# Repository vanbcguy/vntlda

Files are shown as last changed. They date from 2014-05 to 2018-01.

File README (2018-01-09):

vntlda
======

VNT LDA Controller

This software is designed to let you build yourself a VNT controller using an Arduino.  At a minimum you can run this with just a pressure sensor or just a TPS sensor plus an RPM signal, though for actual closed loop control you need all three.  The software will also work with an EGT sensor and can control a second solenoid / device - this can be used to reduce the pressure seen by the LDA when you hit high EGTs thereby reducing fuel, or it could be used to control a water/methanol injector or really do anything you might be able to think of.

Suggested Pressure Sensors
==========================

The included board design is intended to be used with Freescale MPX-series pressure sensors.  Depending on what you want to do you can use either absolute or relative / gauge pressure sensors.  Modern vehicle controls almost universally use absolute pressure sensors - this results in higher gauge pressure numbers at high altitudes providing consistent performance, however that assumes the ECU is controlling other things like fueling too.  I personally have used relative pressure sensors - they will read '0' when off boost just like a traditional boost gauge would.  This is also how wastegate turbos work.  Given that you are building your own controller I'm guessing you aren't trying to comply with strict emissions control regulations so you'll probably find the relative sensors work just fine, plus you'll probably enjoy having all the potential power your vehicle could have at lower altitudes.

Here are some example sensors:

MPX4250DP - 2 port sensor (leave the bottom port open) - max pressure 36 PSI
MPX5500DP - 2 port sensor (leave the bottom port open) - max pressure 72 PSI

Use the lowest value sensor that will meet your needs - don't be tempted to just go for the
"biggest" you can get as the larger the range of the sensor the lower its resolution. I have
used the MPX4250DP for my boost measurements and the MPX5500DP for my EMP measurements.

Suggested TPS Sensor
====================

You need "something" that will provide varying resistance as the accelerator pedal moves.  If you are using this with a Bosch VE/VP style pump there are a few options available.  Some Dodge trucks with Cummins engines and automatic transmissions have a TPS sensor mounted to the pump already - if you control the automatic transmission some other way (like a knob on the dash) then you can use the TPS for this controller.  There are also Land Rover 300 TDI pumps that came with a Bosch TPS to control their EGR system - these should bolt on to most other VE pumps as well.  If you have a 300 TDI with the EGR otherwise removed then you are already most of the way there!  If you have a different style pump then you are on your own - I recommend finding a "cheap" TPS at a parts store that you think you can work with as that way getting replacement parts will be easy.  The Land Rover TPS is frigging expensive to buy new!

Suggested RPM Sensor
====================

The project I based this off of was designed to work with a Honeywell GT101DC.  I used the factory crank position sensor on my VW AHU TDI, this required me to add an extra IC to work with magnetic reluctance sensors.  You can re-use the board design with the Honeywell sensor just by not installing a few components, namely the TI IC and its associated resistors.  Then the Honeywell wire can be connected to the appropriate hole on the board, probably.

Suggested Boost Control Solenoids
=================================

I initially used the readily avaiable GM 3-port boost control solenoids - AC Delco part number 214-474.  They seem to work fine though they are a bit noisy - take care where you mount them (ie don't screw them to the firewall as the noise will drive you nuts).  I have since moved to a VW-style "N75" valve from a Mk4 TDI; these valves are much quieter.

Logging
=======

The system can stream live data via the serial port for logging purposes.  Press the '#' key while connected via serial and the system will start streaming data in this format:

mapCorrected,vntTargetPressure,vntPositionRemapped,tpsCorrected,rpmActual,pidOutput,n75precontrol,vntMinDc,vntMaxDc,mode,targetRatioKp,targetRatioKi,targetRatioKd,boostCalculatedP,boostCalculatedI,boostCalculatedD,temp1,auxOutput,millis( / 10)

The output data can be captured with a tool like 'screen' and logged to disk. It can then be opened directly in a spreadsheet program like LibreOffice or Excel for graphing purposes.

Updates
=======

Patches and updates very welcome! The code is currently "good enough" for to get things done; many improvements could be made. Assistance reducing memory usage, implementing the missing EMP stuff, etc would be well received.

Board Notes
===========

The header for the MAX31855 amplifier board really should be flipped the other way around - I made a mistake on the board layout. This can be overcome by soldering the header and terminals to the opposite side of the MAX31855 board from normal. Everthing works fine this way.

LCD Setup
=========

This program expects to see an Adafruit RGB serial LCD backpack. It also expects the serial LCD backpack to have been configured for 115200 baud already - the display will appear corrupted if the baud rate of the LCD does not match the program rate. While I have tested successfully at 9600 baud (the Adafruit default) by far the longest running part of the program is the actual LCD update routine - while the VNT control stuff takes only a couple of ms (even with lots of float divisions!) the LCD update takes about 26-28ms at 9600 baud. It takes only 2ms at 115200 so your controller will be much happier with the faster rate. Remember it cannot calculate anything while it's writing to the LCD!

To set the baud rate on a fresh serial backpack plug it in via USB. USB doesn't make use of the baud rate so you can set it up no matter what the current settings are. Issue the following commands:

# stty -F /dev/ttyACM0 9600 -parenb cs8 -cstopb -crtscts
# echo -e "\xFE\x39\x08" > /dev/ttyACM0

The baud rate setting is stored on the LCD's EEPROM and will be briefly displayed at startup allowing you to verify the setting was saved successfully.

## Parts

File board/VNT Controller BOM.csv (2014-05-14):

Part | Value | Device | Package | Description | PROD_ID
C1 | 0.33μF | CAPPTH | CAP-PTH-SMALL | Capacitor
C2 | 0.1μF | CAPPTH | CAP-PTH-SMALL | Capacitor
C3 | 470 pF | CAPPTH | CAP-PTH-SMALL | Capacitor
C4 | 470 pF | CAPPTH | CAP-PTH-SMALL | Capacitor
C5 | 0.01 μF | CAPPTH | CAP-PTH-SMALL | Capacitor
C6 | 1.0 μF | CAPPTH | CAP-PTH-SMALL | Capacitor
C7 | 0.01 μF | CAPPTH | CAP-PTH-SMALL | Capacitor
C8 | 1.0 μF | CAPPTH | CAP-PTH-SMALL | Capacitor
C9 | 0.01 μF | CAPPTH | CAP-PTH-SMALL | Capacitor
C10 | 0.01 μF | CAPPTH | CAP-PTH-SMALL | Capacitor
C11 | 0.33 μF | CAP_POLPTH2 | CPOL-RADIAL-10UF-25V | Capacitor Polarized
C12 | 330 pF | CAPPTH | CAP-PTH-SMALL | Capacitor
C14 | 0.1μF | CAPPTH | CAP-PTH-SMALL | Capacitor
C15 | 0.1μF | CAPPTH | CAP-PTH-SMALL | Capacitor
D1 | 1N4001 | DIODEPTH | DIODE-1N4001 | Diode
D2 | 1N4001 | DIODEPTH | DIODE-1N4001 | Diode
IC1 | LM7809 | V_REG_78XXSINK | TO220-IGO | Voltage Regulator
IC2 | LM1815 | DIL14S | SOCKET-14 | Dual In Line / Socket
JP1 |  | M07LOCK_LONGPADS | 1X07_LOCK_LONGPADS | Header 7
JP2 |  | M07LOCK_LONGPADS | 1X07_LOCK_LONGPADS | Header 7
JP3 | EGT | M06SIP_LOCK | 1X06-SIP_LOCK | Header 6
PS1 | MPX4250DP | MPX****-867C-H | 867C-H | Generic MPX pressure sensor
PS2 | MPX5500DP | MPX****-867C-H | 867C-H | Generic MPX pressure sensor
Q1 | MOSFET-NCHANNELFQP30N06L | MOSFET-NCHANNELFQP30N06L | TO220V | Common NMOSFET Parts | TRANS-10060
Q2 | MOSFET-NCHANNELFQP30N06L | MOSFET-NCHANNELFQP30N06L | TO220V | Common NMOSFET Parts | TRANS-10060
R1 | 82K | RESISTORPTH-1/4W-VERT | AXIAL-0.1 | Resistor
R2 | 1K | RESISTORPTH-1/4W-VERT | AXIAL-0.1 | Resistor
R3 | 4.7K | RESISTORPTH-1/4W-VERT | AXIAL-0.1 | Resistor
R4 | 18K | RESISTORPTH-1/4W-VERT | AXIAL-0.1 | Resistor
R5 | 1M | RESISTORPTH-1/4W-VERT | AXIAL-0.1 | Resistor
R6 | 100 | RESISTORPTH-1/4W-VERT | AXIAL-0.1 | Resistor
R7 | 100 | RESISTORPTH-1/4W-VERT | AXIAL-0.1 | Resistor
R8 | 10K | RESISTORPTH-1/4W-VERT | AXIAL-0.1 | Resistor
R9 | 10K | RESISTORPTH-1/4W-VERT | AXIAL-0.1 | Resistor
U$1 | ARDUINO_R3_SHIELD | ARDUINO_R3_SHIELD | UNO_R3_SHIELD | Shield form compatible with the Arduino Uno R3.

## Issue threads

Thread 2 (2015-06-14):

prog_uchar will not work any more

wickeddoc87, 2015-06-14:
Hello,

Nice to see this Project goes forward.
With the new Arduino IDE 1.6.4 "prog_uchar" will not work any more.
I replaced all "prog_uchar" with "const unsigned char".
Like this it is possible to compile the code with the new Arduino IDE, i will see next week if it is working correct.

I have designed a new PCB with SMD technology, If you are interested tell me how i can send it to you.

I have to questions about your code.
What exactly to you mean with EMP and AUX.

Thx alot,

best regards,
Peter

stupa55, 2015-06-15:
Hej there :)

Nice to here you still working on the project. I sold my VNT turbo to a friend along with the Arduino controller and got back a Wastegate turbo. We set it up and using the one old version of the code and it does work great. Setting the VNT with one driver and a passenger is much easier than I done before alone lol :D
Best reagrdsRemi

     wickeddoc87 <notifications@github.com> schrieb am 12:40 Sonntag, 14.Juni 2015:

 Hello, Nice to see this Project goes forward.
With the new Arduino IDE 1.6.4 "prog_uchar" will not work any more.
I replaced all "prog_uchar" with "const unsigned char".
Like this it is possible to compile the code with the new Arduino IDE, i will see next week if it is working correct.I have designed a new PCB with SMD technology, If you are interested tell me how i can send it to you.I have to questions about your code.
What exactly to you mean with EMP and AUX.Thx alot, best regards,
Peter—
Reply to this email directly or view it on GitHub.

wickeddoc87, 2015-06-18:
Does we know us?
Why your frind use the first version now?

@the author
why you use so many floats in your code. I changed all floats to byte, int  and longs. It's not useful to do calculations with floats.  So I try to keep all variables as big as possible and just before we write it to the output  I calculate the true value. Like this I don't need one float at all.

Just in the Part for Human visualisation I use floats for Ki, Kd, kp...

Why you use micros for the RPM Trigger?  Even if you're engine have 10000 RPMs and you use 6 teeth,  the RPM resolution would be still 1ms,  so Millis should be enough.

An older Projects shows me that micros and floats are slowing down the processor extremely.

Best regards
Peter

.

Best regards Peter

wickeddoc87, 2015-06-19:
Hello, it's me again....

You're calculating controls.lastTime with Millis.
Your loop take about 0.56ms.  So as I understand the code controls.lastTime will be almost ever 1 and sometimes 0 if you do the calculation with multiplication 0 integral is 0.  I think at this position we should do the calculation with micros instead of Millis.

Best regards Peter.

stupa55, 2015-06-19:
Hi, there about which code are we talking ??
I haven't written the code I only used it from vanbcguy, the first code I used and that worked good for me was before 24th Dec 2014 :)
I haven't done further inspections cause all in all the DMN code which vanbcguy based on worked also awesome but needed better adaptation. I used the first versions of vanbcguy to compare and it worked much smoother in my opinion.

Remi

     wickeddoc87 <notifications@github.com> schrieb am 11:17 Freitag, 19.Juni 2015:

 Hello, it's me again.... You're calculating controls.lastTime with Millis.
Your loop take about 0.56ms. So as I understand the code controls.lastTime will be almost ever 1 and sometimes 0 if you do the calculation with multiplication 0 integral is 0. I think at this position we should do the calculation with micros instead of Millis. Best regards Peter. —
Reply to this email directly or view it on GitHub.

vanbcguy, 2015-06-19:
millis is not updated when certain other things are happening, micros always is.

The control loop doesn't execute every run, only every 80ms.

very happy to hear about the update for 1.6.4 - I hadn't had a chance to look at that yet.

EMP = exhaust manifold pressure.  I have a sensor on my board for it but I haven't done anything with it yet.  It is only partly there in the code, it is basically unimplemented at the moment.

The AUX output can be used for controlling water/meth, I use it to help limit EGTs by hiding boost from the LDA.  I have it set to start opening a second control solenoid as EGTs approach 800C.

wickeddoc87, 2015-06-19:
thx for explaining.....

RPM Value is unstable the reason for it is a semi. fault.

  if (teethNo > rpmResolution); <--------------- This Semi should not be there.
  {

wickeddoc87, 2015-06-20:
The Arduino does not support an Software pull down on Inputs .. so this will not work

  pinMode(PIN_TPS, INPUT);
  pinMode(PIN_MAP, INPUT);

  digitalWrite(PIN_TPS, LOW); // safety unconnected TPS
  digitalWrite(PIN_MAP, HIGH); // safety unconnected MAP

you have to do the Pulldown external with a resistor 100K maybe.

so the setup can look like this.

  pinMode(PIN_TPS, INPUT);
  pinMode(PIN_MAP, INPUT_PULLUP);

vanbcguy, 2015-06-22:
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

Good catch.  I've updated, will test this afternoon.

Madhair, 2015-07-04:
hi guys

hope ye can help me out here. new to arduino programming etc but very keen to learn. ive been trying to verify the .ino file but a load of the "prog_uchar" errors were coming up so i replaced them with "const unsigned char" as mentioned above and they're all gone now :)

here is the list of errors i have now and im stumped. i cant figure this part out at all :/ any chance of some help?

Arduino: 1.6.5 (Mac OS X), Board: "Arduino Leonardo"

Build options changed, rebuilding all
vnt_lda_myPID_1.ino: In function 'void setPwmFrequency(int, int)':
vnt_lda_myPID_1:384: error: 'TCCR2B' was not declared in this scope
'TCCR2B' was not declared in this scope

cheers in advance :)

Shane

Madhair, 2015-07-04:
think i have it!

bit of info with leonardo having a library compatibility issue here in post 8
http://forum.arduino.cc/index.php?topic=175158.0

i swapped TCCR2B in line 384 to TCCR0B and it verified. ill report back (if ye dont mind :P) during the week when i get the chance to fit to the car :)

vanbcguy, 2015-07-09:
I've committed the prog_uchar change so it's there for everyone. :)

The 'TCCR2B' to 'TCCR0B' change alters the PWM timers.  The 'setPwmFrequency' routine is specifically set up for the regular 'Uno' so it may need adjustment for other boards.  The frequency that's set in my code is correct for the specific GM solenoids I'm using (which like a sllloowww low frequency signal); other solenoids don't necessarily want the same thing.

vanbcguy, 2015-07-09:
@wickeddoc87 - I'd be interested to see your version without using floats so heavily.  I know it's kind of crappy right now.

The main slowdown though is actually updating the LCD - it takes nearly 50ms to update the entire thing.  I recently changed it to update half the screen at a time which got it down to 28ms per update, but that's really what is limiting how fast I can run the loop right now.  I need to spend some time and sort it out so it can just blast out an entire line at once rather than doing so many positioning steps, just haven't had a chance.

wickeddoc87, 2015-07-09:
Good morning,

about Speed... i did same "Benchmarks" with old and new Arduino IDE and relatively simple Code. The Device programmed with the Arduino IDE 1.6.4 works a LOT LOT LOT faster than 1.0.5, maybe you should try an Update.

About the version without float.... i tried a complete other CALC Part Yesterday and "destroyed" the "old code" without doing a new Backup.  i Just have a not finished old Backup...

void processValues() {

  controls.vntMaxDc = mapLookUp(boostDCMax, controls.rpmCorrected, controls.tpsCorrected);
  controls.vntMinDc = mapLookUp(boostDCMin, controls.rpmCorrected, controls.tpsCorrected);

  controls.rpmCorrected = mapValues(controls.rpmActual, 0, settings.rpmMax);
  controls.mapInput = getFilteredAvarage(&mapAvg);
  controls.mapCorrected = mapValues(controls.mapInput, settings.mapMin, settings.mapMax);
  controls.tpsInput = getFilteredAvarage(&tpsAvg);
  controls.tpsCorrected = mapValues(controls.tpsInput, settings.tpsMin, settings.tpsMax);
  controls.empInput = getFilteredAvarage(&empAvg);
  controls.empCorrected = mapValues(controls.empInput, settings.empMin, settings.empMax);
  controls.egtCorrected = mapValues(controls.temp1, settings.egtMin, settings.egtMax);

  // EGT controls
  controls.auxOutput = mapLookUp(auxMap, controls.rpmCorrected, controls.egtCorrected);

  // TODO add RPM hysterisis
  if ( controls.tpsCorrected > 0 ) {
    controls.idling = false;
  }
  else if ( controls.rpmActual < IDLE_MAX_RPM ) {
    controls.idling = true;
  }
  else {
    controls.idling = false;
  }
  unsigned long currentMillis = millis();
  long timeChange = currentMillis - controls.lastTime;

  long error;
  long integral;
  int calc_integral;
  long derivate;

  int controlSpan;
  int scaledInput;
  int scaledTarget;
  int toControlVNT;
  boolean everyThingIsNormal;

 if (!(controls.prevPidOutput >= 254 && error > 0) && !(controls.prevPidOutput <= 0 && error < 0))  everyThingIsNormal == true;
 else  everyThingIsNormal == false;

  /* This is the available span of our DC - we can only go between min and max */
  controlSpan = controls.vntMaxDc - controls.vntMinDc;

  scaledInput = controls.mapCorrected;

  if (scaledInput > 255) scaledInput = 255;
  else if (scaledInput < 0) scaledInput = 0;

  if ((controls.idling)) {
    // If we are at idle then we don't want any boost regardless of map
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
wickeddoc87, 2015-07-09:
I don't know your display,
I use a Sparkfun Serial Display, it works with Baudrates up to 38400

If your Display Update takes 50ms... with Baud 9600 it will only take 13ms with Baud 38400...

wickeddoc87, 2015-08-05:
I found the real Performance Killer!
It is the max31855 library!

The Library works with Floats und is unbelievable slow!
there are other Library's for the max31855!

With deactivated EGT my Code works 3Times Faster....

I Hope this will help you!

Best regards,
Peter

wickeddoc87, 2015-08-05:
Just try...  To see the Difference..

void readValuesEgt() {
 //  controls.temp1 = thermocouple.readCelsius();
  // controls.temp2 = toTemperature(analogRead(PIN_TEMP2)/4);
  controls.temp2 = 0; // disabled for now as we aren't using it

  if (controls.temp1<=0) {
    controls.temp1 = 0;
  }
  else if (controls.temp1 >= settings.egtMax) {
    controls.temp1 = settings.egtMax;
  }

}

vanbcguy, 2015-08-05:
Yes, it's terrible eh? Actually I'm running a patched version of that library that dramatically speeds it up.  There are many delay_ms calls that are slowing things down more than necessary; this code block is the troublemaker - I've changed the delay_ms to delay_us.  I found that I got bad temperature readings unless I increased the delay to 10 us rather than 1 us.

uint32_t Adafruit_MAX31855::spiread32(void) {
  int i;
  uint32_t d = 0;

  if(hSPI) {
    return hspiread32();
  }

  digitalWrite(sclk, LOW);
  _delay_us(10);
  digitalWrite(cs, LOW);
  _delay_us(10);

  for (i=31; i>=0; i--)
  {
    digitalWrite(sclk, LOW);
    _delay_us(10);
    d <<= 1;
    if (digitalRead(miso)) {
      d |= 1;
    }

    digitalWrite(sclk, HIGH);
    _delay_us(1);
  }

  digitalWrite(cs, HIGH);
  //Serial.println(d, HEX);
  return d;
}

I did actually try a few other MAX31855 libraries but the timer settings I use to get the right PWM frequency seem to cause the EGT readings to get cut in half.  This was the only library I could get to spit out the correct value.

vanbcguy, 2017-11-20:
As we've changed MAX31855 libraries, resolved the prog_uchar issues and switched to a totally different PID routine I'm marking this as closed...

Closed 2017-11-20.

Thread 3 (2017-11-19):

CAN BUS communication ?

HaganHao, 2017-11-19:
I have a actuator from Hella, which is defined to communicate with ECU by CAN-BUS.
How can I control my actuator with those code ?

vanbcguy, 2017-11-20:
You would have to build a CANBUS interface; there's nothing in the code designed to do that currently. I believe I have seen CANBUS shields out there however I don't have a CANBUS turbo to test with. Patches happily accepted!

Closed 2017-11-20.

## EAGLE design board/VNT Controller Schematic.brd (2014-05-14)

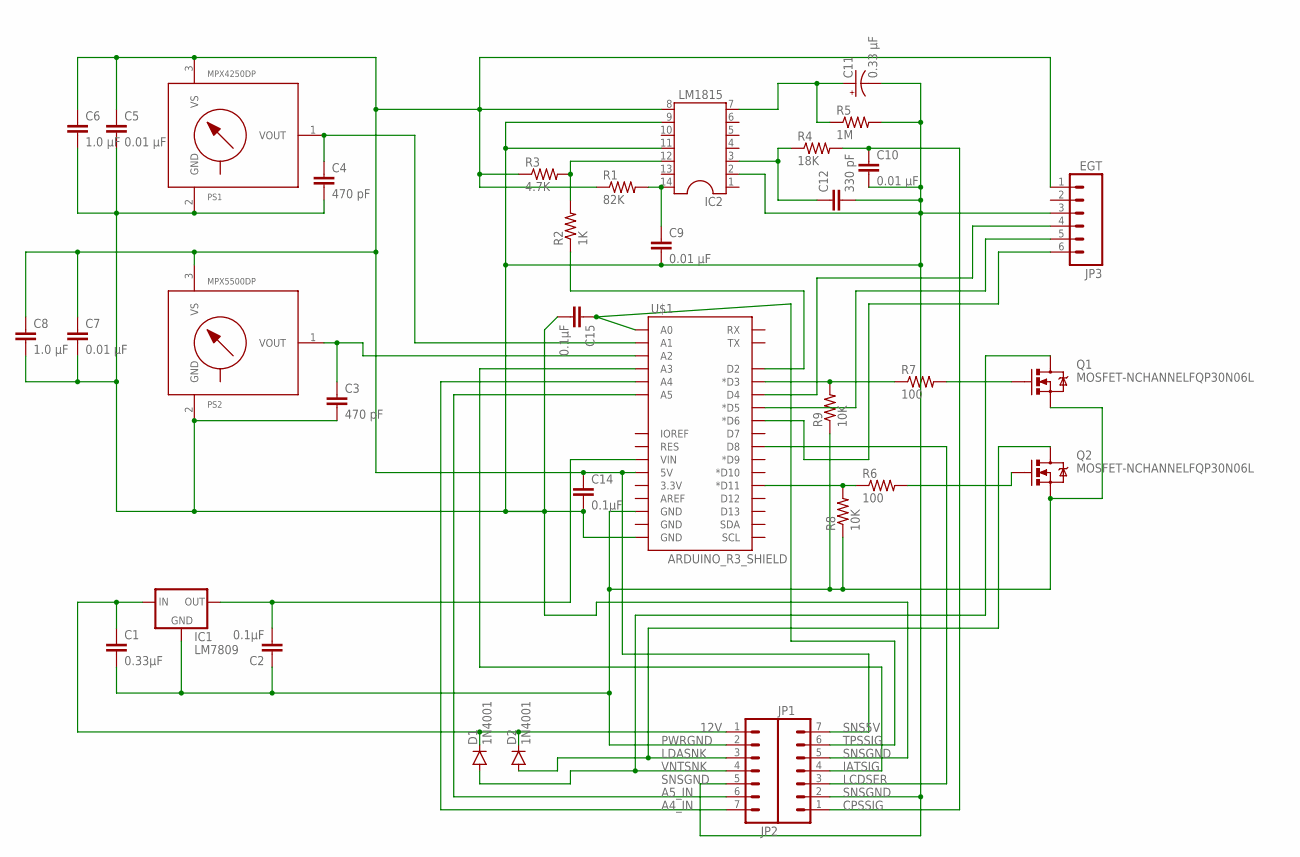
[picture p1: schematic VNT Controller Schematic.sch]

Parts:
C1: 0.33μF; CAP-PTH-SMALL
C2, C14, C15: 0.1μF; CAP-PTH-SMALL
C3, C4: 470 pF; CAP-PTH-SMALL
C5, C7, C9, C10: 0.01 μF; CAP-PTH-SMALL
C6, C8: 1.0 μF; CAP-PTH-SMALL
C11: 0.33 μF; CPOL-RADIAL-10UF-25V
C12: 330 pF; CAP-PTH-SMALL
D1, D2: 1N4001; DIODE-1N4001
IC1: LM7809; TO220-IGO
IC2: LM1815; SOCKET-14
JP1, JP2: M07LOCK_LONGPADS; 1X07_LOCK_LONGPADS
JP3: EGT; 1X06-SIP_LOCK
PS1: MPX4250DP; 867C-H
PS2: MPX5500DP; 867C-H
Q1, Q2: MOSFET-NCHANNELFQP30N06L; TO220V
R1: 82K; AXIAL-0.1
R2: 1K; AXIAL-0.1
R3: 4.7K; AXIAL-0.1
R4: 18K; AXIAL-0.1
R5: 1M; AXIAL-0.1
R6, R7: 100; AXIAL-0.1
R8, R9: 10K; AXIAL-0.1
U$1: ARDUINO_R3_SHIELD; UNO_R3_SHIELD

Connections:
12V: C1.1, D1.C, D2.C, IC1.IN, JP2.1
A4_IN: JP2.7, U$1.A4
A5_IN: JP2.6, U$1.A5
CPSSIG: C10.1, JP1.1, R4.P$2 (2)
IATSIG: JP1.4, U$1.A3
LCDSER: JP1.3, U$1.D8
LDASNK: D2.A, JP2.3, Q2.2 (D)
unnamed: R6.P$1 (1), R8.P$2 (2), U$1.D11 (*D11)
unnamed: C3.1, PS2.1 (VOUT), U$1.A2
unnamed: Q2.1 (G), R6.P$2 (2)
unnamed: IC2.12, R2.P$2 (2), R3.P$2 (2)
unnamed: C4.1, PS1.1 (VOUT), U$1.A1
unnamed: R2.P$1 (1), U$1.D2
unnamed: C9.1, IC2.14, R1.P$2 (2)
unnamed: R7.P$1 (1), R9.P$2 (2), U$1.D3 (*D3)
unnamed: C2.2, IC1.OUT, U$1.VIN
unnamed: Q1.1 (G), R7.P$2 (2)
unnamed: C11.1 (+), IC2.7, R5.P$1 (1)
unnamed: JP3.4, U$1.D4
unnamed: JP3.5, U$1.D5 (*D5)
unnamed: C12.1, IC2.3, R4.P$1 (1)
unnamed: JP3.6, U$1.D6 (*D6)
PWRGND: C1.2, C2.1, IC1.GND, JP2.2, Q1.3 (S), Q2.3 (S), R8.P$1 (1), R9.P$1 (1), U$1.GND@2 (GND)
SNS5V: C5.1, C6.1, C7.1, C8.1, C14.1, IC2.8, JP1.7, JP3.1, PS1.3 (VS), PS2.3 (VS), R1.P$1 (1), R3.P$1 (1), U$1.5V
SNSGND: C3.2, C4.2, C5.2, C6.2, C7.2, C8.2, C9.2, C10.2, C11.2 (-), C12.2, C14.2, C15.2, IC2.2, IC2.9, IC2.11, JP1.2, JP1.5, JP2.5, JP3.3, PS1.2 (GND), PS2.2 (GND), R5.P$2 (2), U$1.GND@0 (GND)
TPSSIG: C15.1, JP1.6, U$1.A0
VNTSNK: D1.A, JP2.4, Q1.2 (D)

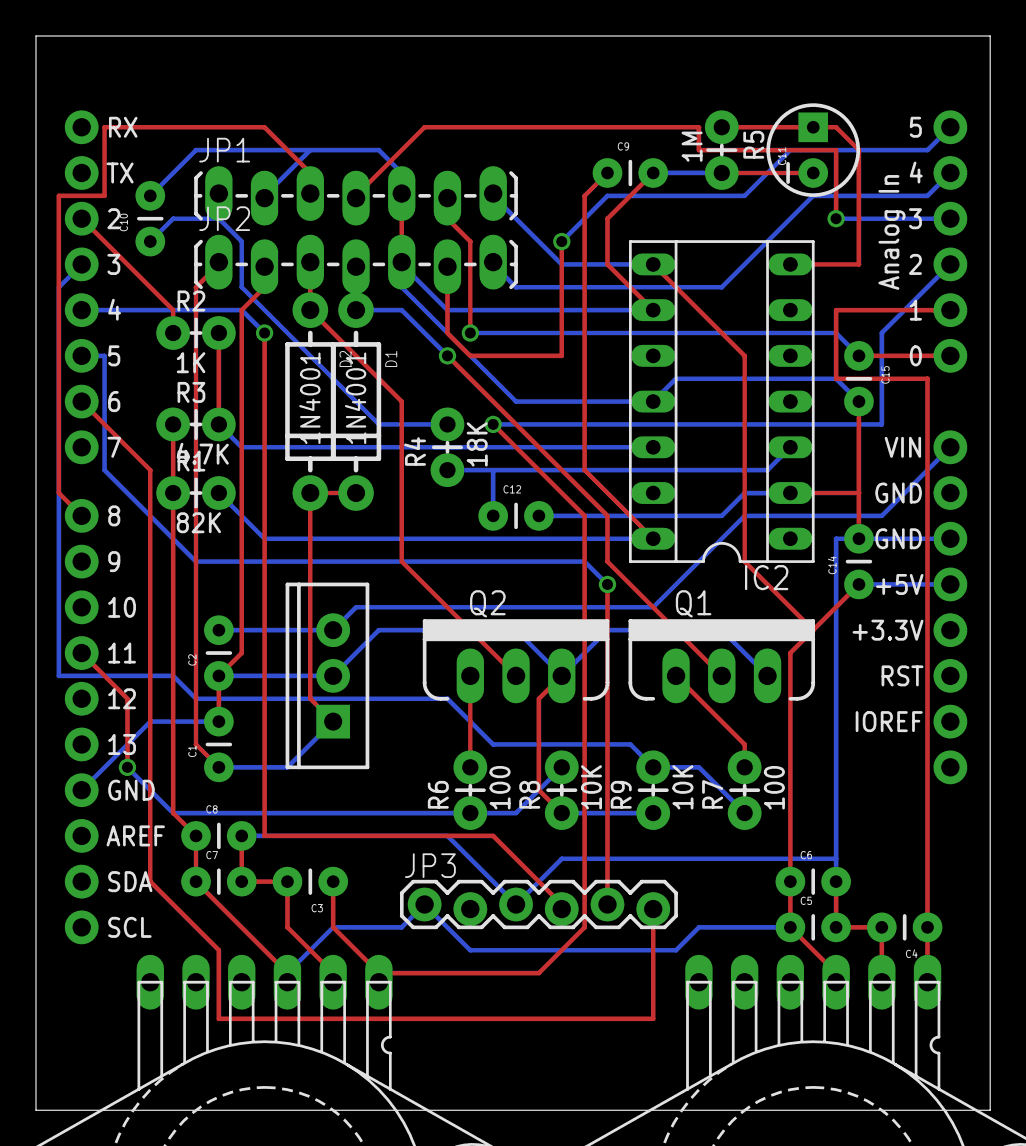
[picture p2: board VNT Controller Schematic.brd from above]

Board: 2 copper layers, 53.0 x 59.7 mm, 35 parts (0 on the bottom side), 27 nets.

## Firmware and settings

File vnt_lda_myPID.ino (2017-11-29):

/*
  Vanbcguy VNT LDA Controller - based on "Standalone VNT Controller" by DMN - http://dmn.kuulalaakeri.org/vnt-lda/
  My current code: https://github.com/vanbcguy/vntlda
  - Rewritten PID loop
  - Support added for EGT probe with LDA control based on EGTs
  - Other various small changes

*/

#include <avr/pgmspace.h>
#include <EEPROM.h>
#include <Wire.h>
#include <SoftwareSerial.h>
#include <SPI.h>
#include <MAX31855.h>    // Use library written for a faster read time - https://github.com/engineertype/MAX31855
#include <ResponsiveAnalogRead.h>
#include <PID_v1.h>

// Also used in NVRAM data store magic header
const unsigned char versionString[] PROGMEM  = "DMN-Vanbcguy Boost Ctrl v3.2.3";

#define PIN_BUTTON A5
#define PIN_HEARTBEAT 13

#define PIN_MAP A1
#define PIN_TPS A0
#define PIN_EMP A2

#define PIN_RPM_TRIGGER 2
#define PIN_VNT_N75 11
#define PIN_AUX_N75 3

#define PIN_LCD 8

#define LCD_BAUD_RATE 115200

// Pins for the EGT MAX31855
#define doPin 4
#define csPin 5
#define clPin 6

ResponsiveAnalogRead map_read(PIN_MAP, false);  // no sleep on the MAP read; need the resolution
ResponsiveAnalogRead tps_read(PIN_TPS, true);
ResponsiveAnalogRead rpm_read(0, true);

// Set up the LCD pin
SoftwareSerial lcd = SoftwareSerial(0, PIN_LCD);

// Set up the thermocouple pins (Adafruit MAX31855 thermocouple interface)
MAX31855 temp(doPin, csPin, clPin );

#define EGT_COOL 165
#define EGT_WARN 700
#define EGT_ALARM 775
#define EGT_MAX_READ 1101

#define IDLE_MAX_RPM 1150
#define MIN_BOOST_SPOOLED 10 // kPa
#define PID_CUT_IN 1520 // rpm
#define TPS_CUT_IN 18 // ~ 7%


/* Scaling factor for your sensors - 255 divided by this should equal the full scale deflection of your sensor */
#define MAP_SCALING_KPA 0.977
#define EMP_SCALING_KPA 1.953

/* Change this if you need to adjust the scaling of the PID outputs - ie if you need finer control at smaller fractional numbers increase this
  or if you need to have large multipliers then decrease this */
#define PIDControlRatio 300

/* The resolution we use to calculate RPM - we are only going to calculate RPM ever 'n' number of teeth that pass by; otherwise we are going to have
  a jittery value.  Divide this value by the 'Teeth per Rotation' setting to know how many revolutions before we caculate RPM. */
#define rpmResolution 30

// Set loop delay times
#define SERIAL_DELAY 107 // ms
#define EXEC_DELAY 50 //ms
#define DISPLAY_DELAY 250 // ms
#define MAP_DELAY 10 //ms


// Calculate Average values
#define AVG_MAX 15

#define MAP_AXIS_TPS 0xDE
#define MAP_AXIS_RPM 0xAD
#define MAP_AXIS_KPA 0xDD
#define MAP_AXIS_CELSIUS 0xAA
#define MAP_AXIS_VOLTAGE 0xAB
#define MAP_AXIS_DUTY_CYCLE 0xAC
#define MAP_AXIS_RAW 0x0
#define MAP_AXIS_EGT 0xAE

/*
  MAP format:

  'M','2','D'   // D - interpolated maps, d - nearest neighbor
  xsize,ysize,x-axis-type,y-axis-type,output-type,
  data[xsize,ysize],
  lastX,lastY,lastRet // automatically filled when used mapLookup

*/

unsigned char auxMap[] = {
  'M', '2', 'D',
  0x6, 0x8, MAP_AXIS_RPM, MAP_AXIS_EGT, MAP_AXIS_DUTY_CYCLE, // 01 - new version
  0, 0, 0, 0, 0, 0,
  0, 0, 0, 0, 0, 0,
  0, 0, 0, 0, 0, 0,
  0, 0, 0, 0, 0, 0,
  0, 0, 0, 0, 0, 0,
  0, 0, 0, 0, 0, 0,
  60, 60, 60, 60, 210, 210,
  210, 210, 210, 210, 210, 210,
  00, 00, 00,                // lastX,lastY,lastRet
};


unsigned char boostRequest[] = {
  'M', '2', 'D',
  0xC, 0xB, MAP_AXIS_RPM, MAP_AXIS_TPS, MAP_AXIS_KPA, // 01 - new version
  0, 0, 0, 15, 34, 44, 46, 46, 46, 43, 39, 37,
  0, 5, 15, 27, 38, 49, 51, 51, 51, 48, 43, 41,
  0, 5, 20, 32, 42, 54, 57, 57, 57, 53, 48, 45,
  0, 5, 20, 40, 55, 60, 63, 63, 63, 59, 53, 50,
  0, 5, 22, 43, 60, 67, 70, 70, 70, 65, 59, 55,
  0, 5, 24, 47, 65, 74, 78, 78, 78, 72, 66, 61,
  0, 6, 27, 58, 75, 92, 98, 98, 98, 90, 83, 76,
  0, 7, 30, 70, 92, 110, 123, 123, 123, 113, 104, 95,
  0, 9, 33, 75, 112, 138, 154, 154, 154, 141, 130, 119,
  0, 11, 41, 87, 128, 173, 193, 193, 193, 176, 162, 149,
  0, 12, 45, 85, 145, 192, 214, 214, 214, 195, 180, 166,
  00, 00, 00,                // lastX,lastY,lastRet
};

unsigned char boostDCMax[] = {
  'M', '2', 'D',
  0x8, 0xB, MAP_AXIS_RPM, MAP_AXIS_TPS, MAP_AXIS_DUTY_CYCLE,
  0, 204, 204, 180, 155, 140, 120, 70,
  0, 204, 204, 180, 155, 140, 120, 70,
  0, 204, 204, 175, 155, 140, 120, 70,
  0, 204, 190, 160, 135, 130, 120, 70,
  0, 204, 185, 160, 135, 130, 120, 70,
  0, 204, 180, 160, 135, 130, 120, 70,
  0, 204, 180, 155, 135, 130, 120, 70,
  0, 204, 175, 150, 135, 130, 120, 70,
  0, 204, 175, 145, 135, 125, 120, 70,
  0, 204, 180, 145, 135, 125, 120, 70,
  0, 204, 185, 145, 135, 125, 120, 70,
  00, 00, 00,                // lastX,lastY,lastRet
};

unsigned char boostDCMin[] = {
  'M', '2', 'D',
  0x9, 0xB, MAP_AXIS_RPM, MAP_AXIS_TPS, MAP_AXIS_DUTY_CYCLE,
  0, 50, 50, 50, 50, 50, 50, 50, 50,
  0, 121, 110, 100, 91, 83, 75, 68, 50,
  0, 121, 110, 100, 91, 83, 75, 68, 50,
  0, 121, 110, 100, 91, 83, 75, 68, 50,
  0, 110, 100, 91, 83, 75, 68, 62, 50,
  0, 99, 90, 70, 70, 70, 70, 65, 50,
  0, 99, 90, 70, 70, 70, 70, 65, 50,
  0, 99, 90, 70, 70, 70, 70, 65, 50,
  0, 99, 90, 70, 70, 70, 70, 65, 50,
  0, 99, 90, 70, 70, 70, 70, 65, 50,
  0, 99, 90, 70, 70, 70, 70, 65, 50,
  00, 00, 00,                // lastX,lastY,lastRet
};

unsigned char n75precontrolMap[] = {
  'M', '2', 'D',
  0xC, 0xB, MAP_AXIS_RPM, MAP_AXIS_TPS, MAP_AXIS_DUTY_CYCLE,
  0, 90, 90, 110, 110, 100, 90, 75, 62, 50, 50, 50,
  0, 204, 204, 204, 182, 163, 145, 130, 122, 115, 106, 70,
  0, 204, 204, 198, 165, 148, 137, 126, 118, 112, 102, 70,
  0, 204, 204, 176, 160, 142, 130, 117, 107, 102, 95, 70,
  0, 204, 204, 145, 124, 115, 109, 101, 94, 87, 82, 70,
  0, 204, 204, 145, 115, 112, 104, 94, 90, 85, 78, 70,
  0, 204, 204, 132, 111, 109, 103, 94, 87, 80, 76, 70,
  0, 204, 204, 132, 110, 108, 102, 94, 86, 80, 76, 70,
  0, 204, 204, 138, 107, 103, 98, 91, 85, 80, 76, 70,
  0, 204, 204, 142, 128, 119, 110, 103, 97, 89, 82, 70,
  0, 204, 204, 160, 150, 140, 132, 121, 110, 98, 86, 70,
  00, 00, 00,              // lastX,lastY,lastRet
};

const unsigned char statusString1[] PROGMEM  = " Active view: ";

#define OPTIONS_VANESOPENIDLE 1
#define OPTIONS_VNTOUTPUTINVERTED 2

// contains configurable data. Can be stored in eeprom
struct settingsStruct {
  int tpsMin;
  int tpsMax;
  int mapMin;
  int mapMax;
  int egtMin;
  int egtMax;
  int empMin;
  int empMax;
  int rpmMax;
  int rpmTeethsPerRotation;
  unsigned char mode;
  char options;
  int boostKp;
  int boostKi;
  int boostKd;
};

settingsStruct settings;

//  contains calculated output data. calculated each run of mainloop
struct controlsStruct {
  // inputs
  volatile int tpsInput;
  unsigned char tpsCorrected;
  volatile int mapInput;
  double mapCorrected;
  volatile int egtInput;
  unsigned char egtCorrected;
  volatile int empInput;
  unsigned char empCorrected;
  char mode; // operating mode

  // outputs

  double vntTargetPressure;
  unsigned char vntPositionRemapped;
  unsigned char vntPositionDC;
  int vntMinDc;
  int vntMaxDc;
  int n75precontrol;

  // calculated value
  volatile int rpmActual;
  volatile unsigned char rpmCorrected;
  unsigned char statusBits;

  bool idling;
  int temp1;

  unsigned char auxOutput;

  float boostCalculatedP;
  float boostCalculatedI;
  float boostCalculatedD;

  double pidOutput;

  unsigned long lastTime;
  float lastInput;
};

controlsStruct controls;


double Kp;
double Ki;
double Kd;

// set up VNT PID control
PID vntPid(&controls.mapCorrected, &controls.pidOutput, &controls.vntTargetPressure, Kp, Ki, Kd, P_ON_E,DIRECT);

struct avgStruct {
  unsigned char pos;
  unsigned char size;
  volatile unsigned int avgData[AVG_MAX];
};

avgStruct mapAvg;

char buffer[100]; // general purpose buffer, mainly used for string storage when printing from flash
unsigned long lastPacketTime;
const unsigned char mapVisualitionHelp[] PROGMEM  = "Top Left is 0,0 (press: L - toggle live mode)";

unsigned char page = 0;
const char *pages[] = {
  "About", "Adaptation", "Actuator Fine-tune", "Edit map: boostRequest", "Edit map: boostDCMin", "Edit map: boostDCMax", "Edit map: n75preControl", "Edit map: Aux. device PWM map", "Output Tests"
};

unsigned char *editorMaps[] = {
  boostRequest, boostDCMin, boostDCMax, n75precontrolMap, auxMap
};

unsigned char clearScreen[] =  {
  27, '[', '2', 'J', 27, '[', 'H'
};

const unsigned char ANSIclearEol[] PROGMEM = {
  27, '[', 'K', 0
};

const unsigned char ANSIclearEolAndLf[] PROGMEM = {
  27, '[', 'K', '\r', '\n', 0
};
const unsigned char ANSIgoHome[] PROGMEM = {
  27, '[', '1', ';', '1', 'H', 0
};
const unsigned char ANSIclearEos[] PROGMEM = {
  27, '[', 'J', 0
};

void setPwmFrequency(int pin, int divisor) {
  byte mode;
  if (pin == 5 || pin == 6 || pin == 9 || pin == 10) {
    switch (divisor) {
      case 1:
        mode = 0x01;
        break;
      case 8:
        mode = 0x02;
        break;
      case 64:
        mode = 0x03;
        break;
      case 256:
        mode = 0x04;
        break;
      case 1024:
        mode = 0x05;
        break;
      default:
        return;
    }
    if (pin == 5 || pin == 6) {
      TCCR0B = TCCR0B & 0b11111000 | mode;
    }
    else {
      TCCR1B = TCCR1B & 0b11111000 | mode;
    }
  }
  else if (pin == 3 || pin == 11) {
    switch (divisor) {
      case 1:
        mode = 0x01;
        break;
      case 8:
        mode = 0x02;
        break;
      case 32:
        mode = 0x03;
        break;
      case 64:
        mode = 0x04;
        break;
      case 128:
        mode = 0x05;
        break;
      case 256:
        mode = 0x06;
        break;
      case 1024:
        mode = 0x7;
        break;
      default:
        return;
    }
    // TCCR2A = 0xA3;
    TCCR2B = TCCR2B & 0b11111000 | mode;
  }
}


volatile unsigned int teethNo = 0;

void rpmTrigger() {
  // increase the tooth count whenever we see a tooth go by
  teethNo++;
}

unsigned long rpmMicros = 0;
unsigned long teethSeconds = 0;

void calcRpm() {
  if (teethNo > rpmResolution)
  {
    int rpm;

    detachInterrupt(0); // don't trigger increments while we're calculating

    teethSeconds = 60000000 / settings.rpmTeethsPerRotation;

    // teethSeconds is one second in microseconds / number of teeth per revolution - avoid overflowing by pre-dividing a second by the number of teeth
    rpm = (teethSeconds * teethNo) / (micros() - rpmMicros);

    // Set time to now, reset tooth count to zero to start incrementing again
    rpmMicros = micros();
    teethNo = 0;

    attachInterrupt(0, rpmTrigger, FALLING); // back to the daily grind

    // controls.rpmActual = (rpmSmoothing * rpm) + ((1.0-rpmSmoothing)*controls.rpmActual);

    rpm_read.update(rpm / 10);
    controls.rpmActual = rpm_read.getValue() * 10;

    if (controls.rpmActual > settings.rpmMax) {
      controls.rpmActual = 0;
    }
  }
}

void gotoXY(char x, char y) {
  Serial.print(F("\e["));
  Serial.print(y, DEC);
  Serial.print(F(";"));
  Serial.print(x, DEC);
  Serial.print(F("H"));
}

void setup_lcd() {
  // Put all the LCD setup stuff here, we will call this from
  // the "setup" loop

  lcd.begin(LCD_BAUD_RATE);

  // set the splash screen
  lcd.write(0xFE);
  lcd.write(0x40);
  strcpy_P(buffer, (PGM_P)&versionString);
  lcd.print(buffer);
  delay(10);


  // set the contrast, 200 is a good place to start, adjust as desired
  lcd.write(0xFE);
  lcd.write(0x50);
  lcd.write(200);
  delay(10);

  // set the brightness - we'll max it (255 is max brightness)
  lcd.write(0xFE);
  lcd.write(0x99);
  lcd.write(255);
  delay(10);

  // set background colour - r/g/b 0-255
  lcd.write(0xFE);
  lcd.write(0xD0);
  lcd.write(64);
  lcd.write(255);
  lcd.write((uint8_t)0);
  delay(10);

  // turn off cursors
  lcd.write(0xFE);
  lcd.write(0x4B);
  lcd.write(0xFE);
  lcd.write(0x54);

  // turn off autoscroll
  lcd.write(0xFE);
  lcd.write(0x52);

  // clear screen
  lcd.write(0xFE);
  lcd.write(0x58);
  delay(10);   // we suggest putting delays after each command

  // go 'home'
  lcd.write(0xFE);
  lcd.write(0x48);
  delay(10);   // we suggest putting delays after each command

  vntPid.SetSampleTime(100);
}

void calcKp() {
  Kp = (float)(settings.boostKp) / PIDControlRatio;
}

void calcKi() {
  Ki = (float)(settings.boostKi) / PIDControlRatio;
}

void calcKd() {
  Kd = (float)(settings.boostKd) / PIDControlRatio;
}

void setup() {
  delay(1500);    // Wait for LCD to actually start up
  setup_lcd();

  Serial.begin(115200);
  Serial.print(F("Boot:"));

  pinMode(PIN_HEARTBEAT, OUTPUT); // DEBUG led

  pinMode(PIN_BUTTON, INPUT); // Reset switch
  digitalWrite(PIN_BUTTON, HIGH);  // activate pull up resistor

  pinMode(PIN_RPM_TRIGGER, INPUT); // Reset switch
  digitalWrite(PIN_RPM_TRIGGER, HIGH); // pullup for honeywell

  attachInterrupt(0, rpmTrigger, FALLING); // or rising!

  setPwmFrequency(PIN_VNT_N75, 128); // was 1024
  setPwmFrequency(PIN_AUX_N75, 128); // was 1024

  pinMode(PIN_VNT_N75, OUTPUT);
  pinMode(PIN_AUX_N75, OUTPUT);

  pinMode(PIN_TPS, INPUT);
  pinMode(PIN_MAP, INPUT);

  digitalWrite(PIN_TPS, LOW); // safety unconnected TPS
  digitalWrite(PIN_MAP, HIGH); // safety unconnected MAP

  // clear screen
  lcd.write(0xFE);
  lcd.write(0x58);

  lcd.print(F("Load:"));
  Serial.print(F("OK, Load:"));
  if (loadFromEEPROM(false) == false) {
    Serial.print(F("invalid conf."));
    lcd.print(F("INVALID CONF"));
    loadDefaults();
    delay(2000);
  }
  else {
    Serial.println(F("OK"));
    lcd.print(F("OK."));
    delay(500);
  }
  Serial.println(F("\r\n"));
  Serial.write(clearScreen, sizeof(clearScreen));

  mapAvg.size = AVG_MAX;

  //initial setup of kp/ki/kd
  calcKp();
  calcKi();
  calcKd();

  digitalWrite(PIN_HEARTBEAT, LOW);

  // set up screen
  layoutLCD();

  pageAbout(1); // force output
}

void loadDefaults() {
  memset(&settings, 0, sizeof(settingsStruct));
  settings.tpsMin = 85;
  settings.tpsMax = 970;
  settings.mapMin = 55;
  settings.mapMax = 975;
  settings.empMax = 1023;
  settings.egtMax = 970;
  settings.egtMin = 0;
  settings.rpmTeethsPerRotation = 4;
  settings.rpmMax = 6000;
  settings.options = 0;
  settings.boostKp = 220;
  settings.boostKi = 7;
  settings.boostKd = 15;
}


unsigned char mapValues(int raw, int mapMin, int mapMax) {
  if (raw < mapMin)
    return 0;
  if (raw >= mapMax)
    return 0xff;

  return map(raw, mapMin, mapMax, 0, 255);
}

unsigned char mapValuesSqueeze(int raw, int mapMin, int mapMax) {
  return map(raw, 0, 255, mapMin, mapMax);
}

unsigned char mapInterpolate(unsigned char p1, unsigned char p2, unsigned char pos) {
  return (p1 * (100 - pos) + p2 * pos) / 100;
}

unsigned char mapLookUp(unsigned char *mapData, unsigned char x, unsigned char y) {
  unsigned char isInterpolated = *(mapData + 2);
  unsigned char tableSizeX = *(mapData + 3);
  unsigned char tableSizeY = *(mapData + 4);
  unsigned char yPos;
  *(mapData + 8 + tableSizeX * tableSizeY) = x;
  *(mapData + 8 + tableSizeX * tableSizeY + 1) = y;

  if (tableSizeY) {
    yPos = y / (256 / (tableSizeY - 1));
  }
  else {
    yPos = 0;
  }
  unsigned char xPos = (x / (256 / (tableSizeX - 1)));
  int ofs = 8; // skip headers

  unsigned char p1 = *(mapData + ofs + (yPos * tableSizeX) + xPos);
  unsigned char p2 = *(mapData + ofs + (yPos * tableSizeX) + (((xPos + 1) >= tableSizeX) ? xPos : xPos + 1));
  unsigned char p3 = *(mapData + ofs + ((((yPos + 1) >= tableSizeY) ? yPos : yPos + 1) * tableSizeX) + xPos);
  unsigned char p4 = *(mapData + ofs + ((((yPos + 1) >= tableSizeY) ? yPos : yPos + 1) * tableSizeX) + (((xPos + 1) >= tableSizeX) ? xPos : xPos + 1));

  unsigned char ret;
  if (isInterpolated == 'D') {
    int amountX = (x % (256 / (tableSizeX - 1))) * (10000 / (256 / (tableSizeX - 1)));
    if (tableSizeY) {
      // 2D
      int amountY = (y % (256 / (tableSizeY - 1))) * (10000 / (256 / (tableSizeY - 1)));
      char y1 = mapInterpolate(p1, p2, amountX / 100);
      char y2 = mapInterpolate(p3, p4, amountX / 100);
      ret = mapInterpolate(y1, y2, amountY / 100);
    }
    else {
      // 1D
      ret = mapInterpolate(p1, p2, amountX / 100);
    }
  }
  else {
    ret = p1;
  }
  *(mapData + 8 + tableSizeX * tableSizeY + 2) = ret;
  return ret;
}


char mapDebugCharValue(unsigned char c) {
  if (c < 5) {
    return ' ';
  }
  else if (c < 20) {
    return '.';
  }
  else if (c < 60) {
    return ':';
  }
  else if (c < 128) {
    return '!';
  }
  else if (c < 180) {
    return 'o';
  }
  else if (c < 220) {
    return 'O';
  }
  else  {
    return '@';
  }
}


// Fetches and print string from flash to preserve some ram!
void printFromFlash(const unsigned char *str) {
  strcpy_P(buffer, (PGM_P)str);
  Serial.print(buffer);
}

int EEPROMwriteData(int offset, byte *ptr, int size) {
  int i;
  for (i = 0; i < size; i++)
    EEPROM.write(offset++, *(ptr++));
  return i;
}

int EEPROMreadData(int offset, byte *ptr, int size) {
  int i;
  for (i = 0; i < size; i++)
    *(ptr++) = EEPROM.read(offset++);
  return i;
}

void saveToEEPROM() {
  int ofs = 0;
  // write magic header
  strcpy_P(buffer, (PGM_P)&versionString);
  ofs += EEPROMwriteData(0, (byte*)&buffer, strlen(buffer));
  // write control struct
  ofs += EEPROMwriteData(ofs, (byte*)&settings, sizeof(settingsStruct));

  ofs += EEPROMwriteData(ofs, (byte*)&auxMap, sizeof(auxMap));
  ofs += EEPROMwriteData(ofs, (byte*)&boostRequest, sizeof(boostRequest));
  ofs += EEPROMwriteData(ofs, (byte*)&boostDCMin, sizeof(boostDCMin));
  ofs += EEPROMwriteData(ofs, (byte*)&boostDCMax, sizeof(boostDCMax));
  ofs += EEPROMwriteData(ofs, (byte*)&n75precontrolMap, sizeof(n75precontrolMap));

  printFromFlash(ANSIclearEolAndLf);
  Serial.print(ofs, DEC);
  Serial.print(F("SAVED "));
  Serial.print(ofs);
  Serial.print(F(" BYTES."));

  delay(1000);
}

bool loadFromEEPROM(bool force) {
  int ofs = 0;
  // if reset pin is active, no not load anything from eeprom
  if (digitalRead(PIN_BUTTON) == 0) {
    Serial.print(F("PIN_BUTTON active.."));
    delay(2000);
    return false;
  }
  // Check magic header to prevent data corruption of blank board or wrong version save file
  if (!force) {
    strcpy_P(buffer, (PGM_P)&versionString);
    for (ofs = 0; ofs < strlen(buffer); ofs++) {
      if (EEPROM.read(ofs) != buffer[ofs])
        return false;
    }
  }
  ofs = strlen(buffer);
  ofs += EEPROMreadData(ofs, (byte*)&settings, sizeof(settingsStruct));

  ofs += EEPROMreadData(ofs, (byte*)&auxMap, sizeof(auxMap));
  ofs += EEPROMreadData(ofs, (byte*)&boostRequest, sizeof(boostRequest));
  ofs += EEPROMreadData(ofs, (byte*)&boostDCMin, sizeof(boostDCMin));
  ofs += EEPROMreadData(ofs, (byte*)&boostDCMax, sizeof(boostDCMax));
  ofs += EEPROMreadData(ofs, (byte*)&n75precontrolMap, sizeof(n75precontrolMap));

  return true;
}


int toKpaMAP(int raw) {
  return raw * MAP_SCALING_KPA;
}

int toKpaEMP(int raw) {
  return raw * EMP_SCALING_KPA;
}

int toRpm(int raw) {
  return round(((float)settings.rpmMax / 255) * (float)raw);
}

int toEgt(int raw) {
  return round(((float)settings.egtMax / 255) * (float)raw);
}

int toTps(int raw) {
  // percent
  return int(raw / 2.55);
}

void printIntWithPadding(int val, unsigned char width, char padChar) {
  // print enough leading zeroes!
  memset(buffer, padChar, 30);
  // append string presentation of number to end
  itoa(val, buffer + 30, 10);
  // print string with given width
  Serial.print(buffer + 30 + strlen(buffer + 30) - width);
}
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
void loop() {

  if ((millis() - mapLoop) >= MAP_DELAY) {
    readValuesMap();  // Read every loop; we're calculating an average to clean up noise.
    mapLoop = millis();
  }

  /* Actual execution will happen every EXEC_DELAY - this is where we do our actual calculations */
  if ((millis() - execLoop) >= EXEC_DELAY) {


    execTimeRead = millis();
    readValuesTps();
    readValuesEgt();
    execTimeRead = millis() - execTimeRead;


    execTimeAct = millis();
    // We will actually process our values and change actuators every EXEC_DELAY milliseconds
    if (freezeModeEnabled) {
      Serial.print(F("\rFREEZE "));
    }
    else {
      // update output values according to input
      calcRpm();
      determineIdle();
      controlVNT();
      controlEGT();
      updateOutputValues();
    }
    execLoop = millis();
    execTimeAct = execLoop - execTimeAct;
  }


  /* we are only going to actualy process every SERIAL_LOOP_DELAY milliseconds though we will read from our sensors every loop
    This way we can get high resolution readings from the sensors without waiting for the actual calculations to occur every
    single time */

  else if ((millis() - serialLoop) >= SERIAL_DELAY) {

    unsigned char data = 0;

    // User interface for configuration and monitoring
    if (Serial.available()) {
      data = Serial.read();
      if (data >= '0' && data <= '9') {
        page = data - '0';
      }
      else if (data == ':') {
        freezeModeEnabled = !freezeModeEnabled;
      }
      else if (data == '#') {
        page = 10;
      }
      else if (data == 27) {
        data = Serial.read();
        if (data == '[') {
          data = Serial.read();
          switch (data) {
            case 'A':
              data = 'k';
              break;
            case 'B':
              data = 'j';
              break;
            case 'C':
              data = 'l';
              break;
            case 'D':
              data = 'h';
              break;

            default:
              data = 0;
          }
        }
      }
    }
    displayPage(page, data);
    serialLoop = millis();
  }

  /* The LCD also takes a while to update; only do the update every DISPLAY_DELAY ms as we don't need a blur where numbers should be */

  else if ((millis() - displayLoop) >= DISPLAY_DELAY) {
    execTimeLcd = millis();
    // We will only update the LCD every DISPLAY_DELAY milliseconds
    updateLCD();
    displayLoop = millis();
    execTimeLcd = displayLoop - execTimeLcd;
  }
}

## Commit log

2014-05-14 Added board design
    [DRILEGEND.CFG, VNT Controller BOM.csv, VNT Controller Schematic.brd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]
2014-05-14 Changed datalogging to print raw values for Kp,Ki,Kd, set scaling as a constant so it can be changed in one place
2014-05-15 Switched to alternate PID sum method. Muuuuch better....
2014-05-16 Fixed EGT map so it actually works
    [vnt_lda_myPID.ino]
2014-05-21 Changed TPS pin settings so we will go to 0 instead of 255 if we are disconnected
2014-05-26 Added visualization for actuator position during output tests
2014-06-11 Changed pullup to make TPS pin read HIGH as it should prevent floating though the system will think it is at WOT when the TPS is unplugged
    [vnt_lda_myPID.ino]
2014-06-11 OK changed TPS pin to LOW as I had to work around a broken wire in my TPS sensor - in this mode the TPS input will float if there is no TPS connected, you may not want this
    [vnt_lda_myPID.ino]
2014-06-25 Revert to 30Hz, otherwise the control range is way too small.
    [vnt_lda_myPID.ino]
2014-06-26 Added time correction factor as our loop can compute differently - this may help stabilize things
    [vnt_lda_myPID.ino]
2014-06-26 Fixed bad declaration for lastTime
    [vnt_lda_myPID.ino]
2014-06-26 Changed to input derivative rather than error derivative
    [vnt_lda_myPID.ino]
2014-06-27 Messing with PID code
2014-06-27 Whoops - suddenly realized Kp would have been integrated the way things were done, fixed
    [vnt_lda_myPID.ino]
2014-06-28 Changed 'idle' method - we now don't execute the loop at all at idle. We just output a 0 from the PID loop while keeping the derivative variables primed in case things are changing
2014-07-04 Increase average samples from 7 to 8
2014-09-28 Typo fix - should learn to verify the damn thing will compile before committing eh...
    [vnt_lda_myPID.ino]
2014-10-01 Change Ki scaling factor as values were too small in settings
    [vnt_lda_myPID.ino]
2014-10-01 Fix issue where integral / derivative time factor not correctly scaled after idling
    [vnt_lda_myPID.ino]
2014-10-09 Added proportional control for Kp the same as we have for Ki. Removed old coarse/fine control code that is no longer needed. Set system to open vanes fully if engine speed exceeds rpmMax as the RPM g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
    [vnt_lda_myPID.ino]
2014-10-17 Logs seem to indicate that proportional control is not working as expected - suspect an issue with how proportion was being calculated
    [vnt_lda_myPID.ino]
2014-10-21 Whoops, helps if you use the correct variable for RPM
    [vnt_lda_myPID.ino]
2014-10-23 Rather than adjusting integral gain we are going to clip the integral based on RPM - that way it will stay in a reasonable range rather than keeping the value needed for low throttle at low RPM
2015-01-13 Major refactoring - hopefully much improved RPM calculation, increased averages for our sensor readings. We now read from the sensors every loop but only do calculations every MAIN_LOOP_DELAY ms rath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
2015-01-14 Moved LCD update to its own timer; don't want LCD update timing to influence control timing.
2015-01-14 Datalogger display was showing raw (0-255) values for sensors rather than toKpa values - hadn't noticed as my 0-250 kPa sensor is very close to 0-255. Changed time field to show 1/100 of a second rat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
2015-01-15 We were doing 3 floating point divides/multiplies every iteration that we didn't need to do; moved them to the setup loop plus will call them when we make changes to Kp/Ki/Kd but otherwise we have no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
    [vnt_lda_myPID.ino]
2015-01-15 delay loops were not working properly due to overflowing integer variables. Changed counters to longs to match the millis timer. Also current LCD display code takes 85ms for future reference, removed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
    [vnt_lda_myPID.ino]
2015-01-16 Actually on second though let's go for 45% for off idle integral; shifts at full throttle would probably be a bad thing with it going to 100%
2015-01-17 Having issue with LCD display, temporarily put setup code back in main loop
    [vnt_lda_myPID.ino]
2015-01-20 We were rolling over our RPM calculations at higher RPMs - this one was tricky; the RPMs reported in the datalogger would be fine since they were from the past run. But when the actual datalogger ran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
    [vnt_lda_myPID.ino]
2015-01-20 First calc revolutions per second then do revolutions per minute; avoid overflowing. Casts weren't working properly, this is actually the same number of operations though it will reduce the resolutio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
    [vnt_lda_myPID.ino]
2015-01-21 Realized teethSeconds would not be updated if changing number of teeth while running, RPM would have been incorrect until the next reboot. Fixed.
    [vnt_lda_myPID.ino]
2015-01-25 Set integral to static value below turbo spool RPM. Once the turbo has spooled we can start integrating. This helps prevent integral windup and the resulting overshooot.
    [vnt_lda_myPID.ino]
2015-01-26 added anti-overshoot code; we'll integrate the derivative when it's steep and we're approaching setpoint
    [vnt_lda_myPID.ino]
2015-01-26 minor change to avoid negative integrals; probably would never happen but let's be sure
    [vnt_lda_myPID.ino]
2015-01-28 Tried playing with some things but going to go a different way; committing now so I can go back. If this doesn't work out, this is the point to return to!
    [vnt_lda_myPID.ino]
2015-01-28 OK significant changes to the control loop; we have a few different cases now. Normal control, Unspooled control, Steep Ramp control. Normal just does ordinary PID. Unspooled uses static values for i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
    [vnt_lda_myPID.ino]
2015-01-28 Let's compare the actual pressure, eh?
2015-01-29 Let's use the correct variable for off-boost calculations eh?
    [vnt_lda_myPID.ino]
2015-01-30 Yeaaah math you do on the side of the road with your takeout in the car doesn't always work right. Some restructuring of the logic and comparisons to make this work properly as everything was bass ac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
    [vnt_lda_myPID.ino]
2015-02-01 Some minor threshold tweaks after logging runs. Tighten up fineControl ratio a bit, widen the 'fast building going to overshoot' band, added additonal mode reporting for 'steep but far' mode as it ac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
    [vnt_lda_myPID.ino]
2015-02-01 Getting too much integral on fast build leading to overshoot and oscilation. Reduce initial off-idle integral and start chopping off integral rather than just freezing it when we are in mode 5 (under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
    [vnt_lda_myPID.ino]
2015-02-02 Added back derivative action in mode 7 (fine control) - May need to think on this some more. Might want to add a case for sharply falling derivatives
2015-02-04 Adafruit MAX31855 libraries added. Discovered that the library as provided takes roughly 68ms to read the EGT probe; The loop has been taking 69ms to complete so we found our big time burgler. The fi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
2015-02-04 Found my error in how I was calling layoutLCD, fixed. Removed unneeded files in the project directory.
    [vnt_lda_myPID.ino]
2015-02-04 Added include for SPI.h as latest MAX31855 library requires it
2015-02-05 RPM settings tweaks; not too much lag, not too jumpy.
    [vnt_lda_myPID.ino]
2015-04-27 Added ability to change Max EGT setting - had missed this previously. Not tested yet as of this commit.
    [vnt_lda_myPID.ino]
2015-06-08 Changed MAX31855 library over to the one written by Rob Tillaart. The Adafruit one reads extremely slowly and causes significant problems. Previously I ran a modified version of the Adafruit one but 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
    [vnt_lda_myPID.ino]
2015-06-08 Hopefully fixed flip flop updates to the LCD
    [vnt_lda_myPID.ino]
2015-06-08 Removed averaging; we are now just looking at straight values. Currently seeing very low EGT values with this library
2015-06-08 Switched to https://github.com/ControlConnection/MAX31855 library
2015-06-08 Reverted to Adafruit library with 10ns delays. Suspect something to do with my PWM timers is causing issues as I get duplicate results to another library with 1ns timings.
    [vnt_lda_myPID.ino]
2015-06-11 Change the logic a bit, hopefully avoid the thrashing we've been seeing right around spoolMinBoost
    [vnt_lda_myPID.ino]
2015-06-22 Minor tuning changes. Decrease aggressiveness of Mode 4 (overshoot). Bug fix for accidental integral going over 1.00
    [vnt_lda_myPID.ino]
2015-07-09 Changed prog_uchar to const unsigned char to allow compiling with Arduino 1.6.x - not tested yet, use at your own risk.
2017-06-09 Board notes added - header for MAX31855 is backwards on the board. Oops.
2017-06-12 Removed some of the old temperature sensor code. Note this version will clear any previously saved settings as the settings structure has been modified.
2017-06-13 Flash the LED on the Arduino when the program is running. Add small delay on startup so the LCD has time to boot
2017-06-13 Continued cleanup; print version string to LCD on startup. Fix spelling of Average that has persisted since initial commit
    [vnt_lda_myPID.ino]
2017-06-13 Print strings from flash; significantly reduces RAM requirements
2017-06-13 Tweaks to the LCD setup routine - somewhat simplified now. Write out the whole initial string rather than just filling in the static bits, that way the LCD populates all at once rather than in stages
2017-06-15 Reduce the complexity of the LCD updating; My attempts to make things faster probably made them slower with all the reposition commands on the regular update. In the event that the LCD briefly lost c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
    [vnt_lda_myPID.ino]
2017-06-15 Minor update to data logging page; it was originally set up to be used with 'meters' for displaying gauges on a laptop screen so there were some serial control characters present. We've been using it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
2017-07-13 Updated timer frequency for VW N75 valve rather than GM one. Should be much quieter though I'm not sure how the VNT solenoid will behave.
2017-07-20 Ignore RPM readings that don't make sense - we seem to get noise when the engine isn't running
    [vnt_lda_myPID.ino]
2017-07-20 Using ResponsiveAnalogRead to filter noisy inputs. Also now correctly handling errors when reading from the MAX31855
    [vnt_lda_myPID.ino]
2017-07-31 Formatting mess cleaned up. Also fixed some serious logic problems
    [vnt_lda_myPID.ino]
2017-08-01 Spelling fix for derivate
    [vnt_lda_myPID.ino]
2017-08-02 Some small changes to improve accuracy; the jump between mode 7 (fine control) and mode 4 (overshoot) was too big; reduce it to something more reasonable. Keep integral at full strength during fine c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
    [vnt_lda_myPID.ino]
2017-08-02 Restore average processing for MAP input; the signal can be a little jumpy at high RPM and it is confusing PID. Let's average it out over 20 readings and read every loop - that should still be quite 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
2017-08-07 Updated PID routines. PID output is now actual duty cycle. Integral will now never exceed max duty cycle and will only go as high as error + integral - derivative = max duty cycle
    [vnt_lda_myPID.ino]
2017-09-22 UNTESTED: New version using Arduino PID library; this will need tuning big time!!
2017-09-23 Was missing map editor for n75precontrol; oops. Removed a bunch of redundant code. Fixed the map editor as it was broken. Jittery values from the MAP sensor are confusing things, smooth it out a bit 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
    [vnt_lda_myPID.ino]
2017-09-24 Change to P_ON_E as I'm seeing excessive pullback from PID before hitting the setpoint currently; suspect that the feed forward approach won't work with P_ON_M as it isn't aware of the changes coming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
    [vnt_lda_myPID.ino]
2017-09-24 Updated default settings. n75 map reviewed after some testing. Still have not tested with PID mode change; this update is based off of logs taken previously
2017-09-25 PID control ratios are now even
2017-09-26 Increasing PID Control ratio; you will need to double your P/I/D values in the settings screen to have the same control as previously
2017-09-26 Switched RPM trigger to falling rather than rising; I'm getting noise on my RPM signal. Have a feeling I flipped a couple capacitors on the board, oops. Maybe this will help?
    [vnt_lda_myPID.ino]
2017-09-26 Disabled PID during pre-spool; don't start till we see 10 kPa from the turbo. You can change the point where it comes alive by altering MIN_BOOST_SPOOLED
2017-09-27 Pretty happy with these default PID settings. More map tweaks...
2017-10-22 hookay broke stuff with the last commit and reverted; reloaded the updated maps here. Switch to P_ON_E, added no-pid RPM cut-in.
    [vnt_lda_myPID.ino]
2017-10-23 Added status bits for min/max control; Added limit checks for PID in case of map programming errors
    [vnt_lda_myPID.ino]
2017-10-23 Bug fix: bad map size for mindc map. Also map updates. Will want to reduce P/I settings
    [vnt_lda_myPID.ino]
2017-10-25 Removed some functions I must have duplicated without understanding; they were never being called. Changed data logging to include min/max/rpm for debugging purposes - there is an issue any time you 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
    [vnt_lda_myPID.ino]
2017-10-25 This has been a bug since day one; if the map was wider than it was tall we were never actually looking at the map data under WOT conditions. I think the stock code was 8x8 maps so it probably never 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
    [vnt_lda_myPID.ino]
2017-11-20 Fixed wrong variable for TPS cut-in; no sense in having PID at near-zero accelerator unless you like wound up integrals. Map updates. Significant increase to boostKp default setting as we're relying 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
    [vnt_lda_myPID.ino]
2017-11-29 Keep PID in during pre-spool conditions but don't integrate

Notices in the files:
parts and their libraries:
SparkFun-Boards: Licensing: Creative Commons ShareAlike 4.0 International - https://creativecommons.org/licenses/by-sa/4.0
